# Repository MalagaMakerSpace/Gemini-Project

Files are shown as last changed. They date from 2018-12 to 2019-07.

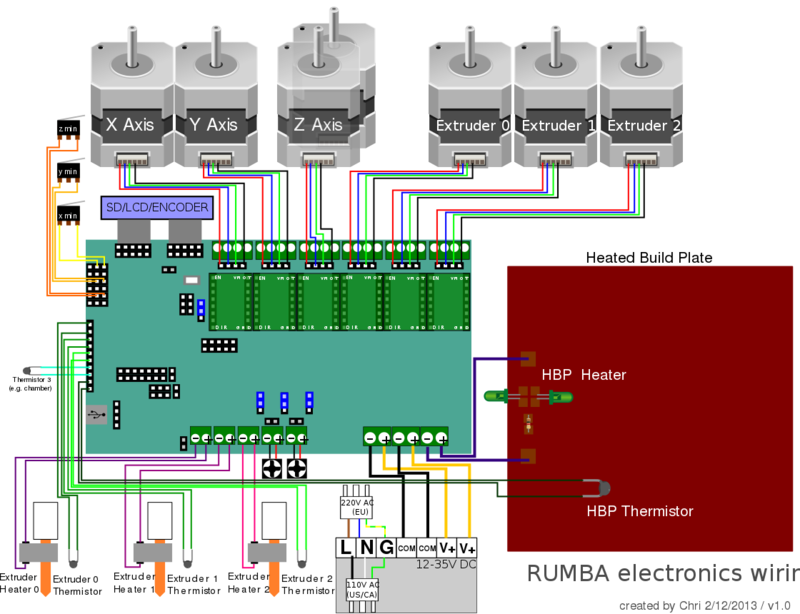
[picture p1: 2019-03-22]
Electronics/Pines Rumba Gráfica.png

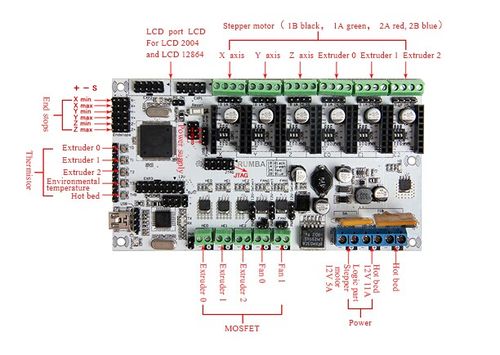
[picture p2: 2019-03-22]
Electronics/Pines Rumba.jpg

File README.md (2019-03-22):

# Gemini-Project
Building a 3D printer with dual independent extruders.

## Main contributors

| Software | Electronics | Y Carriage | Purge & XZ | Documentation  |
|---|---|---|---|---|
| Andrés | Miguel | Pablo V. | Pablo | Idir |
| Ana | Fernando | Ángel | Roberto B. | |
| | Paul | Antonio | | |
| -------------- | -------------- | -------------- | -------------- | -------------- |
| Antonio | Pablo | Miguel | Fernando | Pablo |
| Ángel | Andrés | Andrés | Pablo V | Andrés |
| Fernando | Roberto B. | Roberto B | Antonio | Ana |
| Roberto B | Ana | Andrea V | Miguel | Ángel |
|	 |		  |		 | Andrea V	 |		 |

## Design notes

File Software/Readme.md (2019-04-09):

# Software Section

## Objectives

* Que funcione

## Progress

### Basic Configuration
En el script “Configuration.h”:
* Se define la placa base como RUMBA tomando “MOTHERBOARD 80”.
* Se descomenta la línea "#define REPRAP_DISCOUNT_SMART_CONTROLLER" para activar el LCD.
* Se seleccionan los tipos de sensores térmicos termopares.
	* Según se describe en la documentación, los termistores usados en los extrusores son “de 100 KOhm en resistencia sensible con NTC de 25ºC”. Tal y se indica en el propio script que se está modificando, el valor que se toma para este tipo es “1”. Por ello se marca un 1 en “TEMP_SENSOR_0” y  en "TEMP_SENSOR_1".

### Dual extruder and X axis

En el fichero "Configuration.h":
* Se define el número de extrusores como 2.
* Se descomenta la línea "#define USE_XMAX_PLUG" para usar el final de carrera final del eje X.

En el fichero "Configuration_adv.h":
* Se descomenta la línea "#define DUAL_X_CARRIAGE"
* Para establecer "X2_MIN_POS", se mide la distancia que ocupa el primer extrusor tocando el final de carrera. Como valor final se establece 80 algo superior al real, para asegurarse de que no se tocan.
* Para establecer "X2_MAX_POS", se mide la distancia entre los dos cabezales cuando están "aparcados".
* Como modo de uso se mantiene el que viene por defecto: "DXC_FULL_CONTROL_MODE", cediendo todo el control al gcode.

### Microstep calculation

Componentes relevantes:
* Driver DRV8825 con 32 micropasos
* Motor de 200 pasos por vuelta (1.8º/paso)
* Correa GT2 para ejes X e Y
* Polea 16 dientes para ejes X e Y
* Husillo T8x8 para eje Z (8mm/vuelta)

Usaremos la fórmula:
>	Steps_per_mm = steps_per_revolution / mm_per_revolution

#### Axis X and Y

Steps_per_mm = (32 \* 200) / (16 \* 2) = 200 steps/mm

#### Axis Z

Steps_per_mm = (32 \* 200) / 8 = 800 steps/mm

#### Extruders

TODO: Cálculos provisionales, suponiendo un diámetro de 6mm para la polea

Steps_per_mm = (32 \* 200) / (3.14 \* 6) ~= 340 steps/mm

Se establece con la línea:
> #define DEFAULT_AXIS_STEPS_PER_UNIT   { 200, 200, 800, 340 , 340}
Para poder definir de forma separada los pasos para cada extrusor, se descomenta la línea:
> #define DISTINCT_E_FACTORS

#### Finales de carrera

Los finales de carrera aún no están conectados. El conexionado se puede hacer de forma que:
* Normalmente esté abierto (Interruptor normal)(NO).
* Normalmente cerrado (NC).

Para mayor seguridad, lo ideal sería conectarlos en NC para que en caso de fallo de conexión, la máquina no sea capaz de girar, en lugar de no ser capaz de detectar el pulso de final de carrera.

Marlin por defecto utiliza la configuración NC, por lo que en caso de utilizar esta conexión no habría que invertir la lógica de los finales de carrera. Para ello, se debe asegurar que en el script no estén invertidos e “INVERTING” está en false.

#define X_MIN_ENDSTOP_INVERTING false

#define Y_MIN_ENDSTOP_INVERTING false

#define Z_MIN_ENDSTOP_INVERTING false

#define X_MAX_ENDSTOP_INVERTING false

#define Y_MAX_ENDSTOP_INVERTING false

#define Z_MAX_ENDSTOP_INVERTING false

#define Z_MIN_PROBE_ENDSTOP_INVERTING false

#### SENTIDO DE GIRO DE LOS MOTORES

Se debe considerar que el motor de la cama debe girar en sentido contrario al lógico, pues para avanzar, este motor debe moverse hacia atrás.

Como aún no están conectados, se pueden tomar 2 soluciones: 
* Conectar todos los motores en el mismo sentido y mediante código cambiar el sentido de giro (solución tomada en Marlin).
* Rotar el conector del motor deseado.

Para evitar posibles problemas en el conexionado, lo lógico sería conectar todos los motores de igual modo y mediante el código cambiar el sentido de giro.

Para ello, solo habrá que declarar como “true”: “#define INVERT_Y_DIR true“ (donde Y será el eje en cuestión).

#### AUTOLEVEL

Para implementar el autonivelado, se han descomentado las líneas:

"#define AUTO_BED_LEVELING_BILINEAR", "#define LCD_BED_LEVELING" y "#define PROBE_MANUALLY" 

Para un autonivelado bilinear y para poder controlar la altura de la cama al extrusor durante la calibración.

### CALIBRATION WIZARD

Se está trabajando en un menú para calibrar la impresora mediante un Wizard, similar a la implementada por BCN3D para la Sigma.

Por ahora se ha añadido un menu en el archivo Ultralcd.cpp.

Para buscar como hacer la calibración y la configuración correcta del menú, nos podemos inspirar en el firmware publicado por Prusa y por BCN3D.

## To do

* Comprobar eje Z
* Comprobar pasos por mm de cada eje (Comprobar que se mueve según lo calculado)
* Comprobar especialmente pasos por mm del extrusor.
* Comprobar "X2_MAX_POS", para definir con exactitud esta medida.

## Done

* Comprobar "Invertir la lógica del final de carrera" e "Invertir sentido de giro del motor".
* Configuración del auto nivelado de la cama.
* Comprobar "Invertir la lógica del final de carrera" e "Invertir sentido de giro del motor".
* Decidir que modo de uso del eje X utilizar (FULL_CONTROL, AUTO_PARK o DUPLICATION).

## Pruebas

* 15/03/2019: Software compila correctamente, carga y permite mover eje Z.

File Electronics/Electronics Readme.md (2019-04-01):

# Electronics Section

## Objectives

* Routing wires

## Progress

## Components

* Steppers controller: DRV8825 Stepper Motor Driver Carrier, High Current
* Main Board: https://reprap.org/wiki/RUMBA
* LCD Screen: RepRapDiscount Smart Controller

## Information
* Conectios: https://forum.e3d-online.com/threads/adding-a-fourth-extruder-to-the-rumba.1892/

## Missing components

* Ventilador 1 (H y P): Faltan 4 duponts hembras para los conectores
* Ventilador 2 (H y P): Falta el extensor junto con sus 4 cables para conectarlos a la rumba. (Solo hay unos cables cortos que salen del ventilador, harían falta los cables largos)
* Sensor inductivo: Faltan 3 duponts hembras para conectarlo a la rumba.
* Sensores de temperatura: Harían falta 3 duponts de dobles

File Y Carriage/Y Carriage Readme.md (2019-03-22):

# Y Carriage Section

## Objectives

* Design the bed plate

## Progress

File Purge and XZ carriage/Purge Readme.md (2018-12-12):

# Purge and XZ Carriages Section

## Objectives

* ...

## Progress

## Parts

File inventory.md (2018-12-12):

#Initial inventory

## Spare parts

* RUMBA Board
* 4x Linear bearing with aluminum stands
* 4x Linear guide stands
* 2x Linear guides 12mm
* Power Supply 24V 15A
* Female Plug with switch
* 4x Pololu
* Wires
	1. Two rainbow wires
	2. White wire
	3. 3 black wires

## Printer Parts

* 2x wire holders for extruders
* Aluminum plate for the bed
* Isolation
* Glass
* Heating bed
* 2x wires packs for the motor 
* 7x Steppers
* 2x E3D Volcano extruders
* Main frame
* 2x Linear guides 8mm
* 2x Threaded rods 8mm

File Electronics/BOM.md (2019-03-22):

* Stepper Controller DRV8825: https://www.amazon.es/dp/B06X3VPMGR/ref=twister_B06XHLXXY8?_encoding=UTF8&psc=1
			(Cheap)https://www.amazon.es/Electrely-DRV8825-piezas-disipador-impresora/dp/B07GR5XCYX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

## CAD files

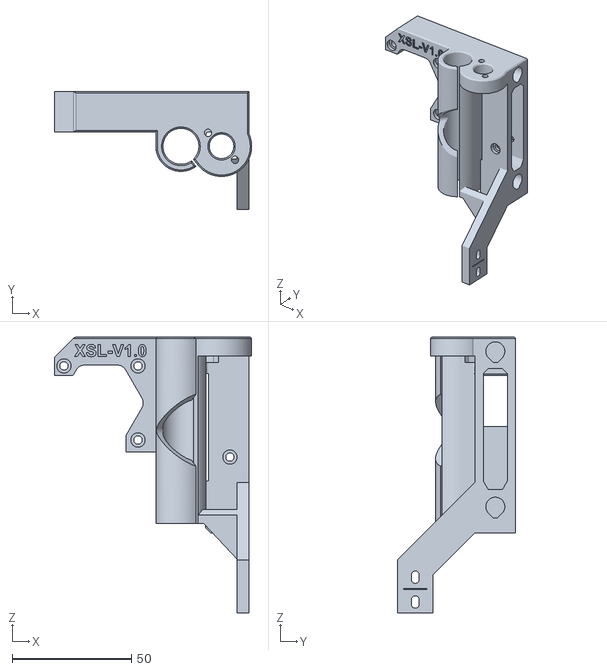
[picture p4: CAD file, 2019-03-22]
Purge and XZ carriage/X axis support left XSL-V1.0.stl
82.6 x 49.5 x 115.5

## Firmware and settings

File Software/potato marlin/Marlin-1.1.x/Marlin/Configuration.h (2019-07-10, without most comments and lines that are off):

#define CONFIGURATION_H
#define CONFIGURATION_H_VERSION 010109
#define MOTHERBOARD 80
#define STRING_CONFIG_H_AUTHOR "(none, default config)" // Who made the changes.
#define SHOW_BOOTSCREEN
#define STRING_SPLASH_LINE1 SHORT_BUILD_VERSION // will be shown during bootup in line 1
#define STRING_SPLASH_LINE2 WEBSITE_URL         // will be shown during bootup in line 2
#define SHOW_CUSTOM_BOOTSCREEN
#define SERIAL_PORT 0
#define BAUDRATE 250000
#define CUSTOM_MACHINE_NAME "PoTaToh MaRlIn"
#define EXTRUDERS 2
#define DEFAULT_NOMINAL_FILAMENT_DIA 1.75
#define POWER_SUPPLY 0
#define TEMP_SENSOR_0 1
#define TEMP_SENSOR_1 1
#define TEMP_SENSOR_2 0
#define TEMP_SENSOR_3 0
#define TEMP_SENSOR_4 0
#define TEMP_SENSOR_BED 1
#define TEMP_SENSOR_CHAMBER 0
#define DUMMY_THERMISTOR_998_VALUE 25
#define DUMMY_THERMISTOR_999_VALUE 100
#define MAX_REDUNDANT_TEMP_SENSOR_DIFF 10
#define TEMP_RESIDENCY_TIME 10  // (seconds)
#define TEMP_HYSTERESIS 3       // (degC) range of +/- temperatures considered "close" to the target one
#define TEMP_WINDOW     1       // (degC) Window around target to start the residency timer x degC early.
#define TEMP_BED_RESIDENCY_TIME 10  // (seconds)
#define TEMP_BED_HYSTERESIS 3       // (degC) range of +/- temperatures considered "close" to the target one
#define TEMP_BED_WINDOW     1       // (degC) Window around target to start the residency timer x degC early.
#define HEATER_0_MINTEMP 5
#define HEATER_1_MINTEMP 5
#define HEATER_2_MINTEMP 5
#define HEATER_3_MINTEMP 5
#define HEATER_4_MINTEMP 5
#define BED_MINTEMP 5
#define HEATER_0_MAXTEMP 275
#define HEATER_1_MAXTEMP 275
#define HEATER_2_MAXTEMP 275
#define HEATER_3_MAXTEMP 275
#define HEATER_4_MAXTEMP 275
#define BED_MAXTEMP 150
#define PIDTEMP
#define BANG_MAX 255     // Limits current to nozzle while in bang-bang mode; 255=full current
#define PID_MAX BANG_MAX // Limits current to nozzle while PID is active (see PID_FUNCTIONAL_RANGE below); 255=full current
#define PID_K1 0.95      // Smoothing factor within any PID loop
#define PID_AUTOTUNE_MENU // Add PID Autotune to the LCD "Temperature" menu to run M303 and apply the result.
#define PID_FUNCTIONAL_RANGE 10 // If the temperature difference between the target temperature and the actual temperature
#define DEFAULT_Kp 22.2
#define DEFAULT_Ki 1.08
#define DEFAULT_Kd 114
#define MAX_BED_POWER 255 // limits duty cycle to bed; 255=full current
#define PREVENT_COLD_EXTRUSION
#define EXTRUDE_MINTEMP 170
#define PREVENT_LENGTHY_EXTRUDE
#define EXTRUDE_MAXLENGTH 200
#define THERMAL_PROTECTION_HOTENDS // Enable thermal protection for all extruders
#define THERMAL_PROTECTION_BED     // Enable thermal protection for the heated bed
#define USE_XMIN_PLUG
#define USE_YMIN_PLUG
#define USE_ZMIN_PLUG
#define USE_XMAX_PLUG
#define ENDSTOPPULLUPS
#define X_MIN_ENDSTOP_INVERTING true // set to true to invert the logic of the endstop.
#define Y_MIN_ENDSTOP_INVERTING true // set to true to invert the logic of the endstop.
#define Z_MIN_ENDSTOP_INVERTING false // set to true to invert the logic of the endstop.
#define X_MAX_ENDSTOP_INVERTING false // set to true to invert the logic of the endstop.
#define Y_MAX_ENDSTOP_INVERTING false // set to true to invert the logic of the endstop.
#define Z_MAX_ENDSTOP_INVERTING false // set to true to invert the logic of the endstop.
#define Z_MIN_PROBE_ENDSTOP_INVERTING false // set to true to invert the logic of the probe.
#define DISTINCT_E_FACTORS
#define DEFAULT_AXIS_STEPS_PER_UNIT   { 100, 100, 800, 160 , 160}
#define DEFAULT_MAX_FEEDRATE          { 200, 200, 5, 25 }
#define DEFAULT_MAX_ACCELERATION      { 3000, 3000, 100, 10000 }
#define DEFAULT_ACCELERATION          3000    // X, Y, Z and E acceleration for printing moves
#define DEFAULT_RETRACT_ACCELERATION  3000    // E acceleration for retracts
#define DEFAULT_TRAVEL_ACCELERATION   3000    // X, Y, Z acceleration for travel (non printing) moves
#define DEFAULT_XJERK                 10.0
#define DEFAULT_YJERK                 10.0
#define DEFAULT_ZJERK                  0.3
#define DEFAULT_EJERK                  5.0
#define Z_MIN_PROBE_USES_Z_MIN_ENDSTOP_PIN
#define PROBE_MANUALLY
#define X_PROBE_OFFSET_FROM_EXTRUDER 10  // X offset: -left  +right  [of the nozzle]
#define Y_PROBE_OFFSET_FROM_EXTRUDER 10  // Y offset: -front +behind [the nozzle]
#define Z_PROBE_OFFSET_FROM_EXTRUDER 0   // Z offset: -below +above  [the nozzle]
#define MIN_PROBE_EDGE 10
#define XY_PROBE_SPEED 8000
#define Z_PROBE_SPEED_FAST HOMING_FEEDRATE_Z
#define Z_PROBE_SPEED_SLOW (Z_PROBE_SPEED_FAST / 2)
#define Z_CLEARANCE_DEPLOY_PROBE   10 // Z Clearance for Deploy/Stow
#define Z_CLEARANCE_BETWEEN_PROBES  5 // Z Clearance between probe points
#define Z_CLEARANCE_MULTI_PROBE     5 // Z Clearance between multiple probes
#define Z_PROBE_LOW_POINT          -2 // Farthest distance below the trigger-point to go before stopping
#define Z_PROBE_OFFSET_RANGE_MIN -20
#define Z_PROBE_OFFSET_RANGE_MAX 20
#define X_ENABLE_ON 0
#define Y_ENABLE_ON 0
#define Z_ENABLE_ON 0
#define E_ENABLE_ON 0 // For all extruders
#define DISABLE_X false
#define DISABLE_Y false
#define DISABLE_Z false
#define DISABLE_E false // For all extruders
#define DISABLE_INACTIVE_EXTRUDER true // Keep only the active extruder enabled.
#define INVERT_X_DIR false
#define INVERT_Y_DIR true
#define INVERT_Z_DIR false
#define INVERT_E0_DIR true
#define INVERT_E1_DIR true
#define INVERT_E2_DIR false
#define INVERT_E3_DIR false
#define INVERT_E4_DIR false
#define X_HOME_DIR -1
#define Y_HOME_DIR -1
#define Z_HOME_DIR -1
#define X_BED_SIZE 200
#define Y_BED_SIZE 200
#define X_MIN_POS 0
#define Y_MIN_POS 0
#define Z_MIN_POS 0
#define X_MAX_POS X_BED_SIZE
#define Y_MAX_POS Y_BED_SIZE
#define Z_MAX_POS 200
#define MIN_SOFTWARE_ENDSTOPS
#define MIN_SOFTWARE_ENDSTOP_X
#define MIN_SOFTWARE_ENDSTOP_Y
#define MIN_SOFTWARE_ENDSTOP_Z
#define MAX_SOFTWARE_ENDSTOPS
#define MAX_SOFTWARE_ENDSTOP_X
#define MAX_SOFTWARE_ENDSTOP_Y
#define MAX_SOFTWARE_ENDSTOP_Z
#define AUTO_BED_LEVELING_BILINEAR
#define ENABLE_LEVELING_FADE_HEIGHT
#define SEGMENT_LEVELED_MOVES
#define LEVELED_SEGMENT_LENGTH 5.0 // (mm) Length of all segments (except the last one)
#define GRID_MAX_POINTS_X 3
#define GRID_MAX_POINTS_Y GRID_MAX_POINTS_X
#define LCD_BED_LEVELING
#define MBL_Z_STEP 0.025    // Step size while manually probing Z axis.
#define LCD_PROBE_Z_RANGE 4 // Z Range centered on Z_MIN_POS for LCD Z adjustment
#define HOMING_FEEDRATE_XY (50*60)
#define HOMING_FEEDRATE_Z  (4*60)
#define EEPROM_SETTINGS // Enable for M500 and M501 commands
#define EEPROM_CHITCHAT   // Give feedback on EEPROM commands. Disable to save PROGMEM.
#define HOST_KEEPALIVE_FEATURE        // Disable this if your host doesn't like keepalive messages
#define DEFAULT_KEEPALIVE_INTERVAL 2  // Number of seconds between "busy" messages. Set with M113.
#define BUSY_WHILE_HEATING            // Some hosts require "busy" messages even during heating
#define PREHEAT_1_TEMP_HOTEND 180
#define PREHEAT_1_TEMP_BED     70
#define PREHEAT_1_FAN_SPEED     0 // Value from 0 to 255
#define PREHEAT_2_TEMP_HOTEND 240
#define PREHEAT_2_TEMP_BED    110
#define PREHEAT_2_FAN_SPEED     0 // Value from 0 to 255
#define PRINTJOB_TIMER_AUTOSTART
#define LCD_LANGUAGE es
#define DISPLAY_CHARSET_HD44780 JAPANESE
#define SDSUPPORT
#define REPRAP_DISCOUNT_SMART_CONTROLLER
#define SOFT_PWM_SCALE 0
#define SERVO_DELAY { 300 }

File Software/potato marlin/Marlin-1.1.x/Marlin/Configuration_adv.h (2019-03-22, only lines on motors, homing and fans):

#define E0_AUTO_FAN_PIN -1
#define E1_AUTO_FAN_PIN -1
#define E2_AUTO_FAN_PIN -1
#define E3_AUTO_FAN_PIN -1
#define E4_AUTO_FAN_PIN -1
#define CHAMBER_AUTO_FAN_PIN -1
#define DUAL_X_CARRIAGE
  #define X2_HOME_DIR 1     // the second X-carriage always homes to the maximum endstop position
  #define X2_HOME_POS X2_MAX_POS // default home position is the maximum carriage position
  #define DEFAULT_DUAL_X_CARRIAGE_MODE DXC_FULL_CONTROL_MODE
#define X_HOME_BUMP_MM 5
#define Y_HOME_BUMP_MM 5
#define Z_HOME_BUMP_MM 2
#define HOMING_BUMP_DIVISOR { 2, 2, 4 }  // Re-Bump Speed Divisor (Divides the Homing Feedrate)
#define MICROSTEP_MODES { 16, 16, 16, 16, 16 } // [1,2,4,8,16]
#define DIGIPOT_I2C_MOTOR_CURRENTS { 1.0, 1.0, 1.0, 1.0, 1.0, 1.0, 1.0, 1.0 }  //  AZTEEG_X3_PRO

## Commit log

2019-03-05 argo illo
    [Configuration.h, Configuration_adv.h]
2019-03-11 Ajustar pasos por mm
    Muchas cositas
    [Configuration.h]
2019-03-15 Trabajo realizado Martes
    [Configuration.h]
2019-03-15 Corregida doble definicion BAUDRATE y STEPS_PER_UNIT doble extrusor
    [Configuration.h]
2019-03-15 Dual X axis
    [Configuration.h, Configuration_adv.h]
2019-03-19 FC y Motores
    Se describen las decisiones tomadas tanto para los finales de carrera como para los sentidos de giro de los motores.
2019-03-22 Ultima Versión Marlin
2019-03-22 cambiado x carriage
    [X axis support left XSL-V1.0.stl]
2019-03-26 Marlin 26/03
    Se ha bajado la velocidad de alimentación del filamento
    [Configuration.h]
2019-04-01 Autolevel
    Implementación autolevel
    [Configuration.h]
2019-07-10 Endstops and steps per mm
    [Configuration.h]

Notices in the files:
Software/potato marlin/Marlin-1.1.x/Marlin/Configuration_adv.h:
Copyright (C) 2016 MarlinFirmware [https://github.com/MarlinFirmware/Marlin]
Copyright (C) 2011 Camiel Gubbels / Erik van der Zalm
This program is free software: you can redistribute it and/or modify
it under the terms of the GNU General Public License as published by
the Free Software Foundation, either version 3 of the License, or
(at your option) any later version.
